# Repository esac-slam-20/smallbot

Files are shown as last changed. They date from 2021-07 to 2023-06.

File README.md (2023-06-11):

# Project-SmallBot

小车制作计划

## 需求

- 带相机，能够图传（回来）
- 带激光雷达，能导航
- IMU？

## 需求分析

1. 算力要足够，所以使用树莓派4B
2. 底盘打算使用3个电机以120度的角度安装全向轮。
3. 树莓派4B的IO口不足以驱动3个电机（6个IO）+3个编码器（3/6个IO，取决于编码器类型），故需要额外单片机
   1. 单片机的电平一般是3.3V的，而驱动控制电平是5V的，所以要做电平转换。
   2. 需要3路PWM和3路正交译码器，这样能够保证最快速度；再加上3/6个GPIO做方向切换。
   3. TB6612好像比L298N好一点，电流也算够，一个电机只要 1 PWM + 2 GPIO 即可。
4. 由于使用了12V的电机，电池组需要使用大于12V的电池，即3*3.7=11.1v（max 13.2v）
   1. 因此，树莓派供电要额外做降压
   2. 也要做充电接口，并且有要充电模块（或者充电器）
   3. 如果放弃外置充电器而使用Type-C，则需要 PD 诱骗器诱骗出15V，共给 SY6912 再接电池供电
   4. 使用动力电池包 or 买动力18650 + 保护板？
5. 激光雷达是5V的，直接从树莓派供电即可；并且走的是串口，直接接就行。
6. 相机图传走Wifi
7. （可选）IMU是I2C接口，并且是3.3V供电，可以直接接树莓派。BMX055看上去够便宜？
8. 单片机的选型
   1. 需要3路PWM和3路正交译码器，这些功能一般由Timer提供
   2. 不要STM32，太贵了
   3. 最终选定 GD32VF103CBT6（开发板），带4路PWM和4路正交译码器，可以最大支持四个电机。

## 硬件版本

| 版本号 | V1 | V2 | V3 |
| ---| --- | --- | --- |
| 日期 | 2021/07 | 2021/09 | 2023/04 |
| 主控 | GD32VF103CBT6(核心板) | GD32VF103CBT6 | CH32V103CBT6 |
| 电机驱动 | TB6612(模块) | TB6612 | DRV8870（AT4950） |
| USB充电 | 是(PD 15V) | 是(宽电压) | 否 |
| IMU | 预留接口 | 预留接口 | 有 |
| 激光雷达 | 无 | 预留接口 | 预留接口 |
| 电机数量 | 4 | 4 | 3+1(舵机) |
| 电池接口 | XT60 | XT60 | XT30 |

## 材料列表

- 主控：树莓派4b, 4G
- 电池：5000mah
- 摄像头：单目/30fps/720p
- 激光雷达：有数据就行
- 电机：普通电机即可，12V
- 轮子：3个全向轮
- 底盘亚克力
- 驱动：TB6612驱动 * 2 = 4路
- 单片机：GD32VF103CBT6（Longan Nano 开发板）

## 价格表

| 物品 | 数量 | 单价 |
| --- | ---- | ---- |
| 树莓派 | 1 | 350  |
| 电池 | 1 | 54 |
| 摄像头 | 1 | 70 |
| 激光雷达 | 1 | 115  |
| 电机 | 3 | 50 |
| 轮子 | 3 | 25 |
| 亚克力底盘 | 1 | 50 |
| 电机驱动 | 2 | 7 |
| 单片机 | 1 | 20 |

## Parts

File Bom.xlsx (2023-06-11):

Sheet: Lite
物品 | 规格 | 数量 | 单价 | 总价 | 备注 | 链接
树莓派 | 4b，2G | 1 | 400 | 400
电池 | 3s, 4000mah | 1 | 50 | 50 | 随便找的
充电器 | - |  |  | 0 | 用PD
电机 | 520 | 3 | 64 | 192 | 加支架 | https://item.taobao.com/item.htm?id=43636856231
轮子 | 58mm | 3 | 44 | 132 | 加轴连器 | https://item.taobao.com/item.htm?id=609475981510&abbucket=15
底盘 | 自己画 | 1 | 50 | 50 | 亚克力切割
驱动 |  | 2 | 8.7 | 17.4 |  | https://item.taobao.com/item.htm?id=558594789309
MCU | GD32VF103CBT6 | 1 | 27 | 27 | 核心板复用 | https://item.taobao.com/item.htm?id=601743142093
 |  |  |  | 0
摄像头 | 720p/30fps | 1 | 70 | 70 | 能用就行
激光雷达 | - | 1 | 115 | 115 | 捡垃圾
IMU | BNO055 | 1 | 58 | 58 |  | https://detail.tmall.com/item.htm?id=611465622037&ns=1&abbucket=15
 |  |  |  | 1111.4

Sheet: Pro
物品 | 规格 | 数量 | 单价 | 总价 | 备注 | 链接
树莓派 | 4b，2G | 1 | 400 | 400
电池 | 3s, 5000mah | 1 | 100 | 100 | 随便找的
充电器 |  | 1 | 38 | 38
电机 | 底盘 | 1 | 369 | 369 |  | https://item.taobao.com/item.htm?id=534516871550
轮子
底盘
驱动 | TB6612 | 2 | 8.7 | 17.4 |  | https://item.taobao.com/item.htm?id=558594789309
MCU | GD32VF103CBT6 | 1 | 27 | 27 | 核心板复用 | https://item.taobao.com/item.htm?id=601743142093
 |  |  |  | 0
摄像头 | 720p/30fps | 1 |  | 0 | 能用就行
激光雷达 | - | 1 |  | 0
IMU | BMX160 | 1 | 99 | 99 |  | https://www.dfrobot.com.cn/goods-2947.html
 |  |  |  | 1050.4

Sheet: IMU比较
型号 | 陀螺仪 |  |  |  |  |  |  |  |  |  |  |  |  | 加速度计
 | 模式 | 量程 (deg/s) | ADC精度 | 初始误差 | 温度误差 (%/K) | 非线性 | 交叉轴灵敏度 | 初始零偏 （Deg/s） | 零偏温飘 （º/s/K） | 线性加速灵敏度 （º/s/g） | RMS (º/s-rms) | 噪声分布 (º/s/√Hz) | 输出 （Hz) | 模式 | 量程 (g) | ADC精度 | 初始误差 | 温度误差 (%/°C) | 非线性 | 交叉轴灵敏度 | 初始零偏 （mg） | 零偏温飘 (mg/K) | 噪声分布 (ug/√Hz) | 输出 （Hz)
MPU-6050 (https://invensense.tdk.com/wp-content/uploads/2015/02/MPU-6000-Datasheet1.pdf) | 0 | ±250 | 16Bits | ±3% | ±2 (ALL) | 0.20% | ±2% | ±20 | ±20 (ALL) | 0.1 | 0.5 | 0.005 | 8000 (MAX) | 0 | ±2 | 16Bits | ±3% | ±0.02% | 0.50% | ±2% | ±50/80 | ±35/60 (mg) | 400 | 1000 (MAX)
 | 1 | ±500 |  |  |  |  |  |  |  |  |  |  |  | 1 | ±4
 | 2 | ±1000 |  |  |  |  |  |  |  |  |  |  |  | 2 | ±8
 | 3 | ±2000 |  |  |  |  |  |  |  |  |  |  |  | 3 | ±16
MPU-9250 (https://invensense.tdk.com/wp-content/uploads/2015/02/PS-MPU-9250A-01-v1.1.pdf) | 0 | ±250 | 16Bits | ±3% | ±4 (ALL) | 0.10% | ±2% | ±5 | ±30 (ALL) | 0.1 | 0.1 | 0.01 | 8000 (MAX) | 0 | ±2 | 16Bits | ±3% | ±0.026% | 0.50% | ±2% | ±60/80 | ±1.5 | 300 | 1000 (MAX)
 | 1 | ±500 |  |  |  |  |  |  |  |  |  |  |  | 1 | ±4
 | 2 | ±1000 |  |  |  |  |  |  |  |  |  |  |  | 2 | ±8
 | 3 | ±2000 |  |  |  |  |  |  |  |  |  |  |  | 3 | ±16
BMI088 (https://www.bosch-sensortec.com/media/boschsensortec/downloads/datasheets/bst-bmi088-ds001.pdf) | 0 | ±125 | 16Bits | ±1% | ±0.03 | 0.05% | ±1% | ±1 | ±0.015 |  | 0.1 |  | 2000 | 0 | ±3 | 16Bits |  | 0.002% | 0.50% | 0.5 | 20 | <0.2 | 160/190 | 1600 (MAX)
 | 1 | ±250 |  |  |  |  |  |  |  |  |  |  | 1000 | 1 | ±6
 | 2 | ±500 |  |  |  |  |  |  |  |  |  |  | 400 | 2 | ±12
 | 3 | ±1000 |  |  |  |  |  |  |  |  |  |  | 200 | 3 | ±24
 | 4 | ±2000 |  |  |  |  |  |  |  |  |  |  | 100

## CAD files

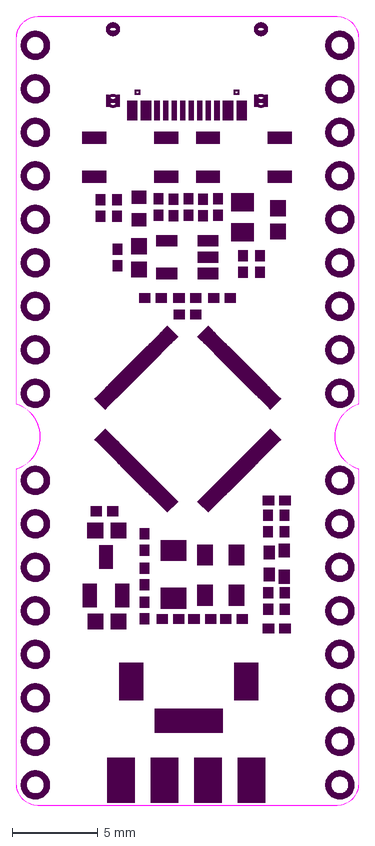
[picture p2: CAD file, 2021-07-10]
Datasheets/主控 - GD32VF103/Longan nano 2663(size).DXF
20.0 x 46.1 mm

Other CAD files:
carCAD/亚克力购买样图.dwg

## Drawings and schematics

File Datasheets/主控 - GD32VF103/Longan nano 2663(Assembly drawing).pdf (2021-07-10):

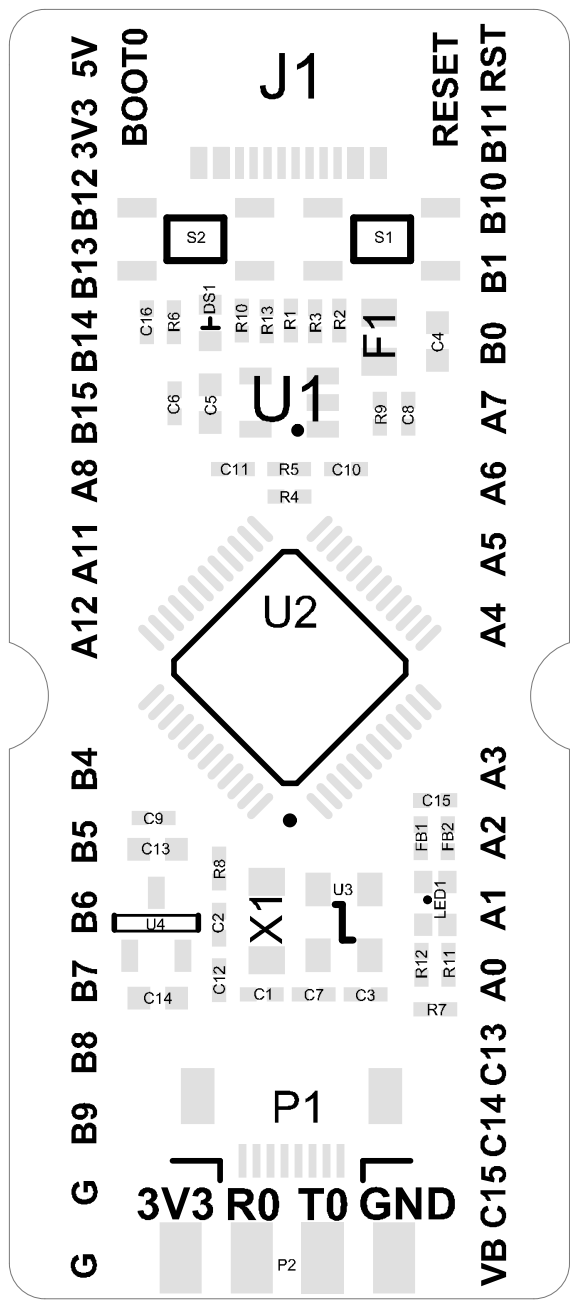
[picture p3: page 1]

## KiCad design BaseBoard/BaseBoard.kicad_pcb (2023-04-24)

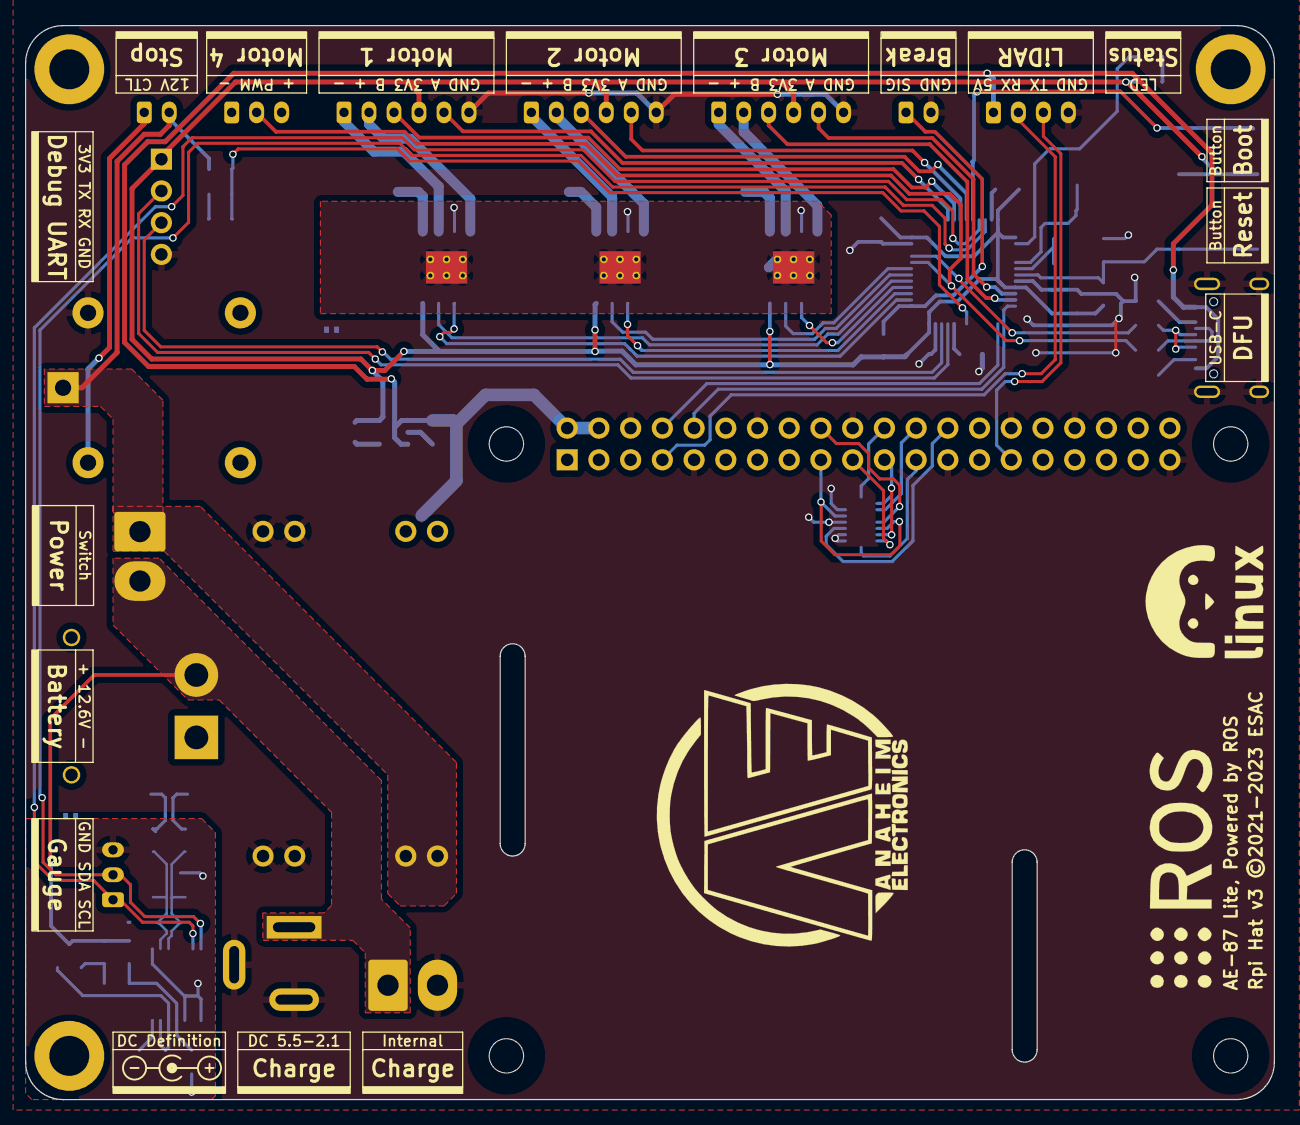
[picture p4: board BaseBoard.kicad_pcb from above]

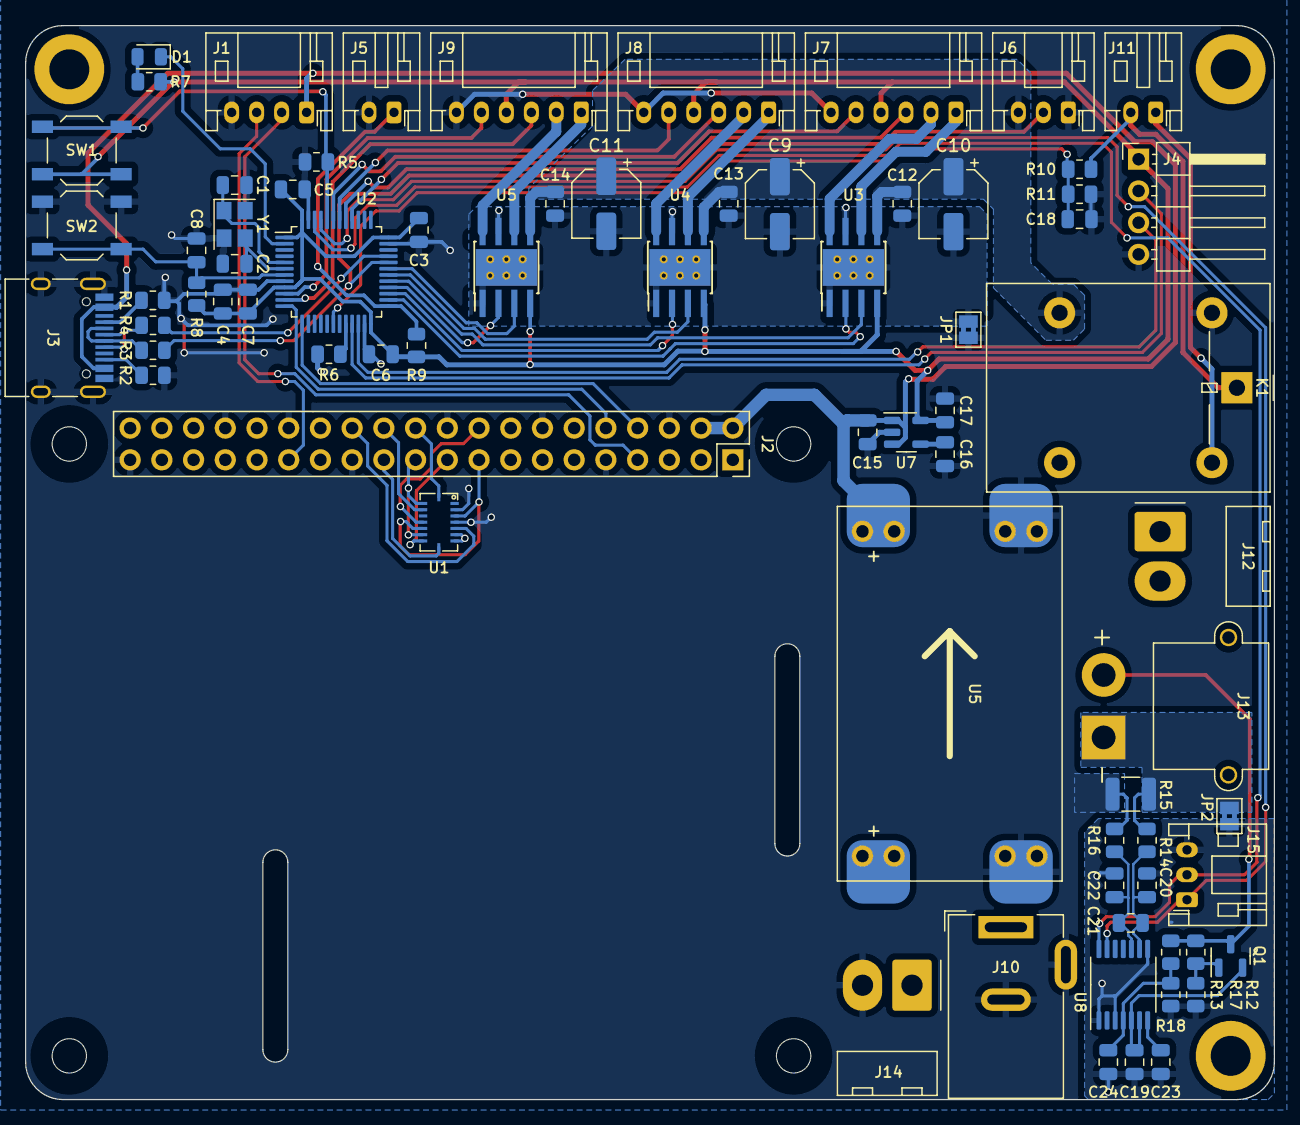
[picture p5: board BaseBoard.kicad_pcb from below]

Board: 2 copper layers, 100.0 x 86.0 mm, 76 parts (73 on the bottom side), 66 nets.

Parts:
C1, C2: 12pF; C_0805_2012Metric
C3, C4, C5, C6, C7, C8, C12, C13, C14, C16, C18, C19, C20, C21, C22, C23: 100nF; C_0805_2012Metric
C9, C10, C11: 47uF; CP_Elec_5x5.4
C15, C17: 1uF; C_0805_2012Metric
C24: 3.3nF; C_0805_2012Metric
D1: LED_White; LED_0805_2012Metric
J1: PH2.0_1x04; JST_PH_S4B-PH-K_1x04_P2.00mm_Horizontal
J2: Raspberry_Pi_2_3; PinSocket_2x20_P2.54mm_Vertical
J3: USB_C_Receptacle_USB2.0; USB_C_Receptacle_HRO_TYPE-C-31-M-12
J4: PinHeader_2.54_1x04; PinHeader_1x04_P2.54mm_Horizontal
J5, J11: PH2.0_1x02; JST_PH_S2B-PH-K_1x02_P2.00mm_Horizontal
J6, J15: PH2.0_1x03; JST_PH_S3B-PH-K_1x03_P2.00mm_Horizontal
J7, J8, J9: PH2.0_1x06; JST_PH_S6B-PH-K_1x06_P2.00mm_Horizontal
J10: DC5.5/2.1; BarrelJack_Wuerth_6941xx301002
J12, J14: HT396R_1x02; Molex_KK-396_A-41792-0002_1x02_P3.96mm_Horizontal
J13: XT30PW; AMASS_XT30PW-M_1x02_P2.50mm_Horizontal
JP1, JP2: NC; SolderJumper-2_P1.3mm_Bridged2Bar_Pad1.0x1.5mm
K1: SRD-12V; Relay_SPDT_Omron-G5LE-1
LOGO1: Logo_ROS; ROS_LOGO_20x6
LOGO2: Logo_Linux; Linux_12x12
LOGO3: Logo_Anaheim_Electronic; Anaheim_Electronic_20
Q1: 2N7002; SOT-23
R1, R2: 5.1k; R_0805_2012Metric
R3, R4: 22R; R_0805_2012Metric
R5, R6, R7, R8, R9: 10k; R_0805_2012Metric
R10: 360k; R_0805_2012Metric
R11, R13: 100k; R_0805_2012Metric
R12, R17: 220k; R_0805_2012Metric
R14, R16: 100R; R_0805_2012Metric
R15: 10mR; R_1210_3225Metric
R18: 16.5k; R_0805_2012Metric
SW1, SW2: TL3342; SW_SPST_TL3342
U1: BMI088; Bochs_LGA16_2x7+2x1
U2: GD32VF103C8Tx; LQFP-48_7x7mm_P0.5mm
U3, U4, U5#2: DRV8870DDA; Texas_HTSOP-8-1EP_3.9x4.9mm_P1.27mm_EP2.95x4.9mm_Mask2.4x3.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
U5: MINI560; Converter_DCDC_Mini_560
U7: SGM2028-3.3YN5G; SOT-23-5
U8: BQ34Z100; TSSOP-14_4.4x5mm_P0.65mm
Y1: 8MHz; Crystal_SMD_3225-4Pin_3.2x2.5mm

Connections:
+3.3VA: J2.1 (3V3), J2.17 (3V3), U1.3 (VDD), U1.11 (VDDIO)
+3V3: C3.1, C4.1, C5.1, C6.1, C7.2, C17.1, J4.1, J7.4, J8.4, J9.4, R7.1, R8.2, R9.1, SW1.2, U2.1 (VBAT), U2.9 (VDDA), U2.24 (VDD), U2.36 (VDD), U2.48 (VDD), U3.4 (VREF), U4.4 (VREF), U5#2.4 (VREF), U7.5 (OUT)
+5V: C15.1, J1.1, J2.2 (5V), J2.4 (5V), J3.A4 (VBUS), J3.A9 (VBUS), J3.B4 (VBUS), J3.B9 (VBUS), U5.3 (OUT), U7.1 (IN), U7.3 (EN)
+12V: J11.2, J12.1, K1.1, R10.1, U5.1 (IN)
+12VA: C9.1, C10.1, C11.1, C12.1, C13.1, C14.1, J6.3, K1.3, U3.5 (VM), U4.5 (VM), U5#2.5 (VM)
+BATT: J10.1, J12.2, J13.2, J14.1, Q1.3 (D), R12.1, R17.1
-BATT: J13.1, JP2.1 (A), R14.2, R15.1
/ADC: C18.1, R10.2, R11.1, U2.18 (PB0)
/BOOT0: R5.1, SW1.1, U2.44 (BOOT0)
/BOOT1: R6.1, U2.20 (PB2)
/BREAK: J5.1, R9.2, U2.25 (PB12)
/CTL_RX: J2.8 (GPIO14/TXD), U2.13 (PA3)
/CTL_TX: J2.10 (GPIO15/RXD), U2.12 (PA2)
/DEBUG_RX: J4.3, U2.22 (PB11)
/DEBUG_TX: J4.2, U2.21 (PB10)
/ENC1_A: J7.5, U2.40 (PB4)
/ENC1_B: J7.3, U2.41 (PB5)
/ENC2_A: J8.5, U2.42 (PB6)
/ENC2_B: J8.3, U2.43 (PB7)
/ENC3_A: J9.5, U2.10 (PA0)
/ENC3_B: J9.3, U2.11 (PA1)
/I2C_SCL: J15.1, U2.45 (PB8), U8.13 (P4/SCL)
/I2C_SDA: J15.2, U2.46 (PB9), U8.14 (P3/SDA)
/IMU_INT1: J2.22 (GPIO25), U1.16 (INT1)
/IMU_INT2: J2.18 (GPIO24), U1.12 (INT3)
/LIDAR_RX: J1.2, J2.7 (GCLK0/GPIO4)
/LIDAR_TX: J1.3, J2.29 (GCLK1/GPIO5)
/Motor/MOT1_N: J7.1, U3.6 (OUT1)
/Motor/MOT1_P: J7.2, U3.8 (OUT2)
/Motor/MOT2_N: J8.1, U4.6 (OUT1)
/Motor/MOT2_P: J8.2, U4.8 (OUT2)
/Motor/MOT3_N: J9.1, U5#2.6 (OUT1)
/Motor/MOT3_P: J9.2, U5#2.8 (OUT2)
/OSCIN: C1.1, U2.5 (PD0), Y1.1
/OSCOUT: C2.1, U2.6 (PD1), Y1.3
/PWM1: U2.29 (PA8), U3.3 (IN1)
/PWM1_ON: U2.26 (PB13), U3.2 (IN2)
/PWM2: U2.30 (PA9), U4.3 (IN1)
/PWM2_ON: U2.27 (PB14), U4.2 (IN2)
/PWM3: U2.31 (PA10), U5#2.3 (IN1)
/PWM3_ON: U2.28 (PB15), U5#2.2 (IN2)
/PWM4: J6.2, R3.1, U2.32 (PA11)
/Power/CTRL: J11.1, K1.5
/Power/SRN: C21.2, C22.1, R16.1, U8.10 (SRN)
/Power/SRP: C20.1, C21.1, R14.1, U8.9 (SRP)
/SPI_CLK: J2.23 (SCLK0/GPIO11), U1.8 (SCL/CLK)
/SPI_CS1: J2.24 (~CE0/GPIO8), U1.14 (CSB1)
/SPI_CS2: J2.26 (~CE1/GPIO7), U1.5 (CSB2)
/SPI_MISO: J2.21 (MISO0/GPIO9), U1.10 (MISO2), U1.15 (MISO1)
/SPI_MOSI: J2.19 (MOSI0/GPIO10), U1.9 (SDA/MOSI)
/USB_DP: R4.1, U2.33 (PA12)
GND: C1.2, C2.2, C3.2, C4.2, C5.2, C6.2, C7.1, C8.2, C15.2, C16.2, C17.2, C18.2, J1.4, J2.6 (GND), J2.9 (GND), J2.14 (GND), J2.20 (GND), J2.25 (GND), J2.30 (GND), J2.34 (GND), J2.39 (GND), J3.A1 (GND), J3.A12 (GND), J3.B1 (GND), J3.B12 (GND), J3.S1 (SHIELD), J4.4, J5.2, J6.1, J7.6, J8.6, J9.6, J10.2, J10.3, J14.2, JP1.1 (A), K1.2, R1.1, R2.1, R5.2, R6.2, R11.2, R15.2, R16.2, SW2.2, U1.2 (NC), U1.4 (GNDA), U1.6 (GNDIO), U1.7 (PS), U2.8 (VSSA), U2.23 (VSS), U2.35 (VSS), U2.47 (VSS), U5.2 (GND), U7.2 (GND), Y1.2, Y1.4
GNDA: C19.2, C20.2, C22.2, C23.2, C24.2, J15.3, JP2.2 (B), R13.2, R18.2, U8.1 (P2), U8.3 (P1), U8.8 (VSS)
GNDPWR: C9.2, C10.2, C11.2, C12.2, C13.2, C14.2, JP1.2 (B), U3.1 (GND), U3.7 (ISEN), U3.9 (GND), U4.1 (GND), U4.7 (ISEN), U4.9 (GND), U5#2.1 (GND), U5#2.7 (ISEN), U5#2.9 (GND)
unnamed: D1.2 (A), R7.2
unnamed: D1.1 (K), U2.2 (PC13)
unnamed: J3.A5 (CC1), R1.2
unnamed: J3.B5 (CC2), R2.2
unnamed: J3.A6 (D+), J3.B6 (D+), R4.2
unnamed: J3.A7 (D-), J3.B7 (D-), R3.2
unnamed: Q1.1 (G), R12.2, R13.1
unnamed: C19.1, Q1.2 (S), U8.5 (CE), U8.6 (REGIN)
unnamed: C8.1, R8.1, SW2.1, U2.7 (NRST)
unnamed: C16.1, U7.4 (BP)
unnamed: C24.1, R17.2, R18.1, U8.4 (BAT)
unnamed: C23.1, U8.7 (REG25)

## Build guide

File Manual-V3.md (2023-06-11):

# 小车使用手册

## 硬件

### 总览

本小车主控由两部分组成，它们是：树莓派和驱动板。

驱动板囊括了电池监控电路、降压电路、电机驱动电路等，板载了IMU。

### 接口与LED说明

[这里应该有一张图]

驱动板：

- Status 主控工作指示灯
- Charge 充电接口
  - 此接口直接与电池并联
  - 需要使用外部充电器接入此接口对电池充电
  - 请勿直接接入12V电源充电
- Battery 电池接口
  - 电池接口为XT30接口
- Gauge 电量计配置口
  - 用于连接外部配置工具，配置电量计内部数据
- Stop 应急开关接口
  - 此开关控制电机驱动的驱动电源，断开后电机会停止供电
- Break 刹车信号
  - 用于控制电机，触发后会将电机设置为刹车状态
- Power 系统总开关
  - 此开关控制电路总电源。
- Lidar 激光雷达接口
  - 与树莓派的 TX（GPIO5）、RX（GPIO4）相连
- Motor1~3 电机接口
  - 用于控制已有的电机
- Motor4 预留电机接口
  - 提供PWM信号和12V电源，用于连接舵机
- Debug UART 调试接口
  - 提供了主控的调试串口
- DFU 烧录接口
  - 用于升级主控程序
- Boot 按键
  - 进入DFU烧写模式
  - 在断电的情况下按住此按键并插入通电，或在通电的情况下按住此按键的同时按下RESET按键，即可进入DFU烧写模式更新固件。
- Reset 按键
  - 按下此按键即可重启主控。
- 主控与树莓派通过串口连接，占用GPIO14、GPIO15（默认串口）
- 主控板载IMU占用SPI0（GPIO7-11），GPIO25（INT1），GPIO24（INT2）

### 方向定义

我们定义主控板方向为后方向，以主控板所在方向的轮子作为后轮。

轮子编号如下：
- 左前轮：3号
- 右前轮：2号
- 后轮：1号

安装完毕后，1-3号电机连接线长度应当是从短到长。

### 变更记录

自V2以来的变更：
- 移除了锂电池充电电路
  - 现在需要外部充电器对电池充电
- 增加了锂电池电量监控电路
- 将5V供电替换为模块，不再使用分立器件
- 替换了电机驱动芯片，降低了发热。
  - 因硬件限制，不再支持四路电机控制输出，仅支持3路电机控制输出
  - 预留一路PWM信号，提供给可能的云台电机使用
- 增加刹车信号输入功能
- 将IMU改为板载
- 修改了大部分接口的位置
  - 接口现在全部为反装，降低整体高度
  - 将树莓派IO放置于外部，方便插线

### 兼容性问题列表

- 修正了V2板子螺丝孔位偏移的问题
  - 因此无法兼容原有机械结构
- 由于接口位置变更，现在
- 上一版本中的预留IMU接口为I2C，此版本改为SPI
- 激光雷达串口由GPIO8/9变更为GPIO4/5

## 软件

### 基础设置

#### 启用控制板连接串口

使用编辑器打开 `/boot/config.txt`，在后面添加下面的指令，启用树莓派的串口：

```
dtoverlay=uart0
dtoverlay=disable-bt
enable_uart=1
```

接着，使用编辑器打开 `/boot/cmdline.txt`，删除前面的
```
console=serial0,115200
```

保存后重启即可以启用树莓派的控制串口。串口设备路径为`/dev/ttyAMA0`

#### 启用激光雷达连接串口

使用编辑器打开 `/boot/config.txt`，在后面添加下面的指令，启用树莓派的串口：

```
dtoverlay=uart3
```

保存后重启即可以启用树莓派的UART3，其引脚为GPIO4、GPIO5，串口设备路径为`/dev/ttyAMA1`

### 高级

#### 热点

// T.B.D.

- [Ref 1](https://www.raspberrypi.org/forums/viewtopic.php?t=211542)
- [Ref 2](https://raspberrypi.stackexchange.com/questions/37920/how-do-i-set-up-networking-wifi-static-ip-address-on-raspbian-raspberry-pi-os/37921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)
- [Ref 3](https://www.raspberrypi.org/documentation/configuration/wireless/access-point-routed.md)

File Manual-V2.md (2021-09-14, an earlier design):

# 小车使用手册

## 硬件

### 总览

本小车主控由两部分组成，它们是：树莓派和驱动板。

驱动板囊括了充电电路、降压电路、电机驱动电路等。

### 接口与LED说明

[这里应该有一张图]

驱动板：

- D1：红色，充电指示灯（充电中）
- D2：绿色，充满指示灯（充满）
- D5：白色，主控工作指示灯
- Charge 充电接口。
  - 此接口可以直接外接电源，通过板载的充电电路对电池充电。
  - 如果你已经有充电器了，请不要通过此接口充电
  - 此接口与Type-C充电接口并联，请不要同时使用此接口和Type-C充电接口
  - 输入电压范围：11.5V-12.5V
- USB Type-C 充电接口（靠近电池侧）
  - 可以接入支持 USB PD / QC 协议的充电器对电池充电。
  - 此接口会自动与PD协议协商，以获取 12V 的电源，故充电器需要支持 12V 输出。
  - 若充电器不支持12V快充输出，协商会自动回退至5V。此时无法正常为电池充电。
- Battery 电池接口
  - 电池接口为XT60接口
  - 旁边的DC接口为5.5-2.1接口，其与电池接口直接并联，用于连接外部充电器直接为电池充电
- Stop 应急开关接口
  - 此开关控制电机驱动的驱动电源，断开后电机会停止供电
- Switch 系统总开关
  - 此开关控制电路总电源。
- IMU 接口：预留，与树莓派相连。
  - 接口定义：3V3、GND、SCL（GPIO3）、SDA（GPIO2）、GPIO22、GPIO23、GPIO24、GPIO25
  - 接口定义与BMX160模块一致，也能兼容大部分IMU模块。
- Lidar 接口：预留，与树莓派相连。
  - 接口定义：5V、TX（GPIO9）、RX（GPIO8）、GND
- Motor1~4 电机接口：用于连接电机。
- 调试接口：提供了主控的调试串口，位于继电器旁边
- USB Type-C 烧录接口：用于升级主控程序。
- BOOT0按键：进入DFU烧写模式。
  - 在断电的情况下按住此按键并插入通电，或在通电的情况下按住此按键的同时按下RESET按键，即可进入DFU烧写模式更新固件。
- RESET按键：重启主控
  - 按下此按键即可重启主控。
- 主控与树莓派通过串口连接，占用GPIO14、GPIO15.

### 方向定义

我们定义主控板方向为后方向，以主控板所在方向的轮子作为后轮。

轮子编号如下：
- 左前轮：3号
- 右前轮：2号
- 后轮：1号

安装完毕后，1-3号电机连接线长度应当是从短到长。

## 软件

### 基础设置

#### 启用控制板连接串口

使用编辑器打开 `/boot/config.txt`，在后面添加下面的指令，启用树莓派的串口：

```
dtoverlay=uart0
enable_uart=1
```

保存后重启即可以启用树莓派的控制串口。串口设备路径为`/dev/ttyAMA0`

#### 启用激光雷达连接串口

使用编辑器打开 `/boot/config.txt`，在后面添加下面的指令，启用树莓派的串口：

```
dtoverlay=uart4
```

保存后重启即可以启用树莓派的UART4，其引脚为GPIO8、GPIO9，串口设备路径为`/dev/ttyAMA1`

### 高级

#### 热点

// T.B.D.

- [Ref 1](https://www.raspberrypi.org/forums/viewtopic.php?t=211542)
- [Ref 2](https://raspberrypi.stackexchange.com/questions/37920/how-do-i-set-up-networking-wifi-static-ip-address-on-raspbian-raspberry-pi-os/37921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)
- [Ref 3](https://www.raspberrypi.org/documentation/configuration/wireless/access-point-routed.md)

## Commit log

2021-07-01 更新 'README.md'
2021-07-01 添加需求分析和物料列表
2021-07-10 完成主控板的绘制，添加一些数据手册
    [BaseBoard.kicad_pcb, BaseBoard.sch, Longan nano 2663(size).DXF]
2021-07-13 添加BOM，板子上添加IMU接口
    [BaseBoard.kicad_pcb, BaseBoard.sch, Bom.xlsx]
2021-07-14 更新线路板布局
    [BaseBoard.kicad_pcb, BaseBoard.sch]
2021-07-23 更新线路板设计，添加PD芯片
    [BaseBoard.kicad_pcb, BaseBoard.sch]
2021-07-23 更新BOM
    [Bom.xlsx]
2021-07-26 添加树莓派的数据手册
2021-07-27 修正一处电阻阻值错误的问题
    [BaseBoard.sch]
2021-08-02 添加使用手册
2021-08-02 更新 'Manual.md'
    添加串口的启用说明
2021-08-04 添加小车方向定义说明
2021-08-05 更新 'Manual.md'
2021-08-10 v2板临时提交
    [BaseBoard.kicad_pcb, BaseBoard.sch, Motor.sch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]
2021-08-28 v2提交
    [BaseBoard.kicad_pcb, BaseBoard.sch, Motor.sch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]
2021-08-29 添加备份封装库
2021-09-01 Modify some footprints.
    [BaseBoard.kicad_pcb, BaseBoard.sch, Power.sch]
2021-09-09 修正两处电阻阻值不正确的问题
    [BaseBoard.kicad_pcb, Power.sch]
2021-09-14 添加V2版本主控说明书
2022-06-29 V3 Baseboard
    [BaseBoard.kicad_pcb, BaseBoard.kicad_sch, BaseBoard.sch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]
2023-03-12 使用功率地
    [BaseBoard.kicad_pcb, BaseBoard.kicad_sch, Motor.kicad_sch]
2023-04-07 临时提交
    [BaseBoard.kicad_pcb, BaseBoard.kicad_sch, Motor.kicad_sch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]
2023-04-09 更新V3线路板
    [BaseBoard.kicad_pcb, BaseBoard.kicad_sch, Motor.kicad_sch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]
2023-04-09 添加v3初版设计
    [BaseBoard.kicad_pcb, BaseBoard.kicad_sch, Motor.kicad_sch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]
2023-04-19 调整孔位置
    [BaseBoard.kicad_pcb]
2023-04-24 修改部分封装和值
    [BaseBoard.kicad_pcb, BaseBoard.kicad_sch, Motor.kicad_sch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]
2023-06-11 Update documents
    [Bom.xlsx]
2023-06-11 docs: add CH32V103 datasheets
    [Longan nano 2663(size).DXF]

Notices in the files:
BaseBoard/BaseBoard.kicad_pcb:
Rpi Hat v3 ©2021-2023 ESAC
